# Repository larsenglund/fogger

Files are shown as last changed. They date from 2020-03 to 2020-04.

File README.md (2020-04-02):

# Fogger
A cheap DIY fog machine with automatic temperature control, display and WiFi remote control.

## Hardware
### Bill of materials
The basic fog machine consists of
* Grill lighter, $15
* Copper fuel pipe (6mm outer diameter, 5m long), $22
* Thermocouple thermometer, $4
* Pump (self priming, 6mm outer diameter inlet and outlet, 12V), $4
* 12V adapter, $3
* PVC tube (5mm inner diameter), $3
* Aluminium foil
* Metal wire
* Rockwool insulation
* About 1 liter of sand

Total cost: $51 (assuming you have the last four items on the list, if not rockwool might be the hardest to come by in small quantities)

The upgraded version with automatic temperature control, display and WiFi remote control removes the "manual" thermocouple thermometer and adds these things:
* Wemos D1 mini (ESP8266) $3
* MAX6675/MAX31855 Module + K Type Thermocouple, $5
* 2 channel relay module (3.3V), $3
* 5V charger, $2
* OLED display (0.91", 128x32, I2C), $2
* 10K thermistor + 47k resistor
* Thermal fuse (~150C, 250V, 10A)

Total cost for upgraded version: $62

Fog juice (smoke liquid) is made from
* Destilled water (4L), $4
* Glycerol (1L), $16

Total cost for 5L of 20% fog juice: $20

Fog juice can also be bought premade for about the same price but then you can't vary the concentration as easy.

### Assembly

Some of the stuff needed

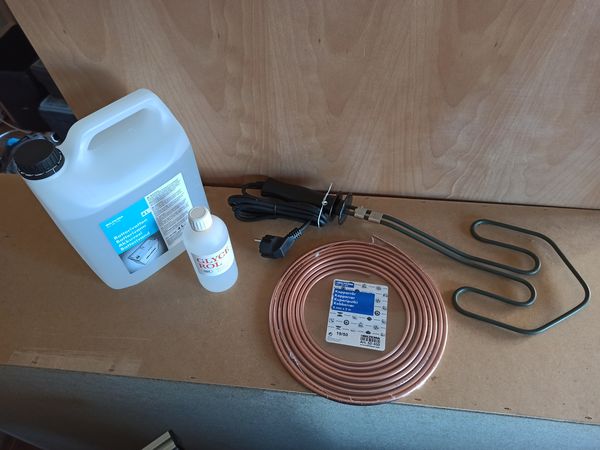
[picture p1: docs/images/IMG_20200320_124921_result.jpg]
Materials


Carefully bend the copper pipe to follow the shape of the grill lighter. Mine was able to go three loops along the whole heater element with a few decimeters to spare on each end. I used cable ties to keep the pipe in place as I was bending it.

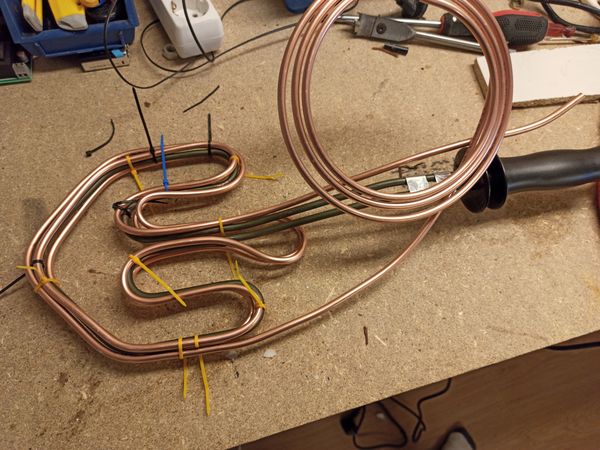
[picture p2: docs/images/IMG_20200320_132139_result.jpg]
Bending


The cable ties are replaced with a tight wiring of metal wire.

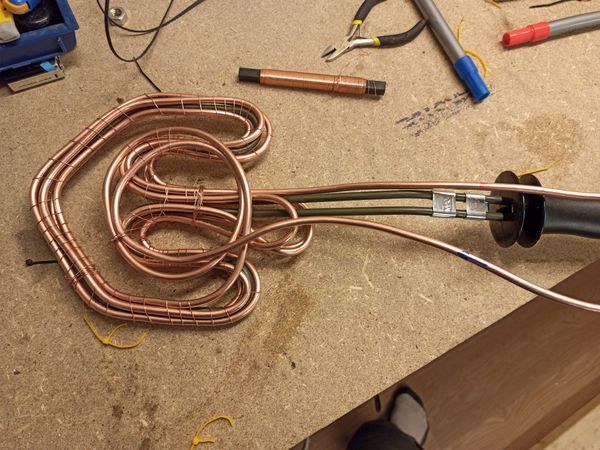
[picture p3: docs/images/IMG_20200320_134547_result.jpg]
Wiring


The thermocouple is wired so that the business end is close to the center of the heater without touching any metal. Then the whole thing is placed on a sheet of rockwool (5-10cm thick) and sand is poured ontop (to act as heat distribution and storage). The rockwool is then folded over to make a insulated package and the whole thing is wrapped in aluminium foil.

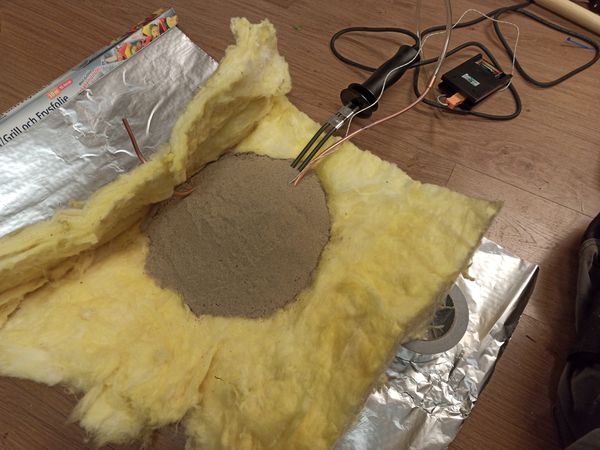
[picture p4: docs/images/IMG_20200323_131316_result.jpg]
Sand


Connect the outlet of the pump to the copper pipe using a PVC tube and on the inled put another tube that leads to a container of fog juice. For the manual version you then plug in the heater and when the temperature reaches 260 degrees celcius on the thermocouple thermometer you can turn off the heater. Turn on power to the pump for a while and enjoy the smoke! When the temperature drops below 250 degrees again you can plug the heater in for a while until it reaches 260 degrees again. The system has quite a bit of thermal lag so if you turn off the heater at 260 degrees it overshoots to about 295 degrees in my setup.

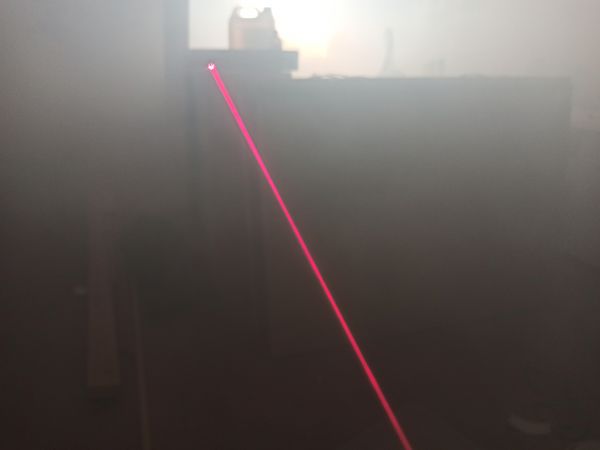
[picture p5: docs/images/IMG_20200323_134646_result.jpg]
Pewpew


Video of first testrun.

(http://www.youtube.com/watch?v=uRvGTlmDHWQ "DIY smoke machine test")

## Electronics
Wiring of components

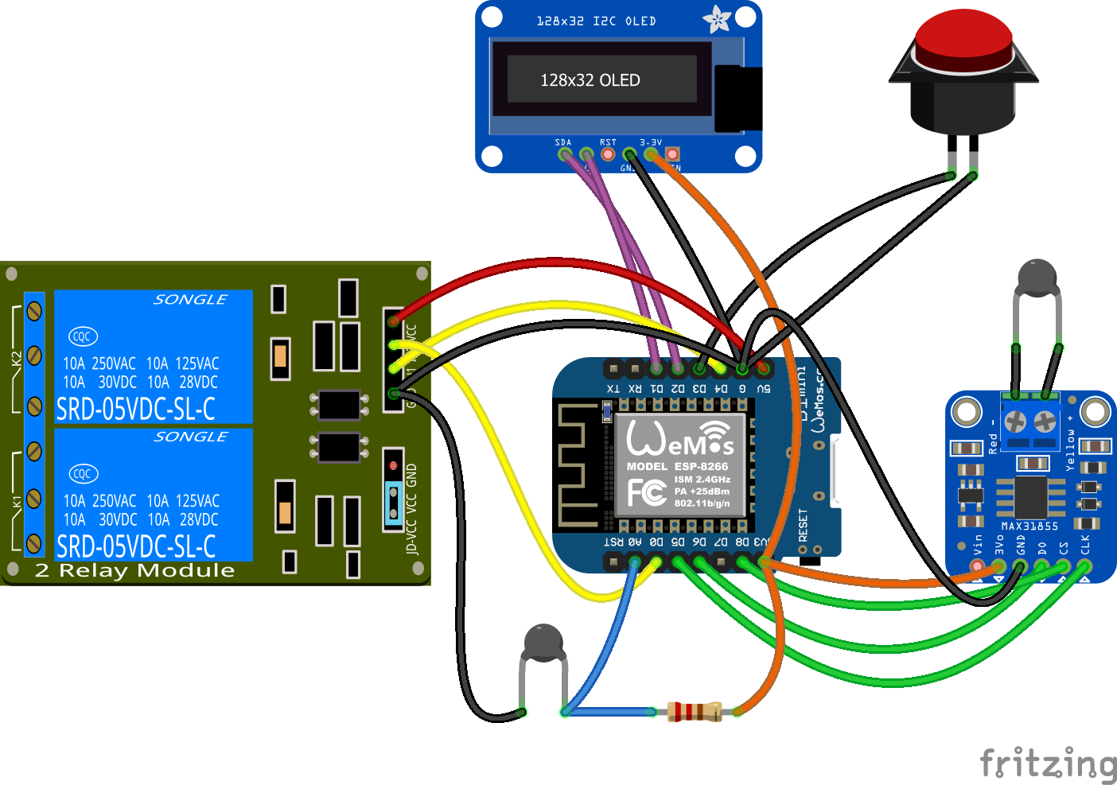
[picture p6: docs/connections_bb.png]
Connections


The heater is connected to channel 1 of the relay board and the pump to channel 2. A 10K thermistor is connected to A0.
The thermal fuse is placed on the incoming live wire.

Pin selection was made using this information.

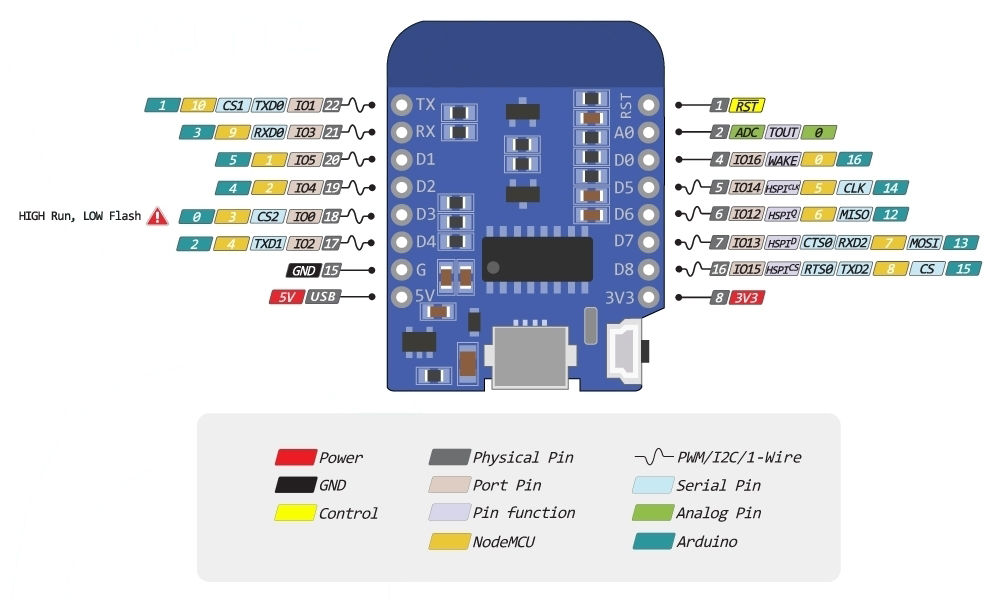
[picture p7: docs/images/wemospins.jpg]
Wemos pins


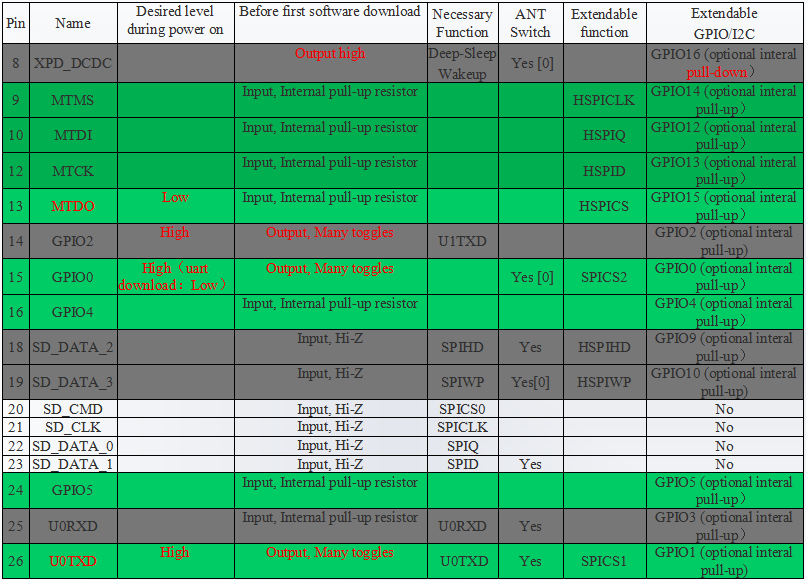
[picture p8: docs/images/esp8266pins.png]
ESP8266 pins


## Software
Software for the Wemos is created with PlatformIO and serves up a captive portal that's used for remote control.

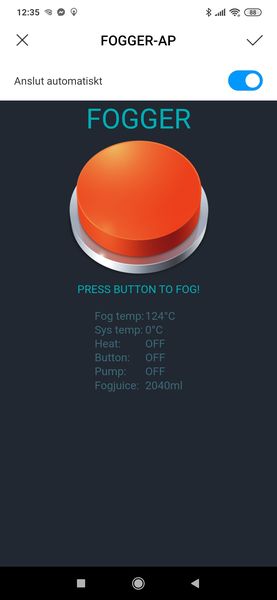
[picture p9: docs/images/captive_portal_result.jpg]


The OLED displays the same information as the captive portal.

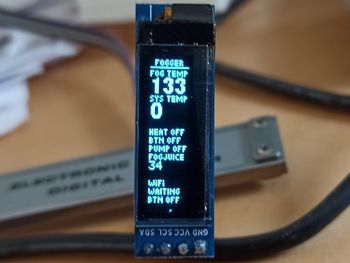
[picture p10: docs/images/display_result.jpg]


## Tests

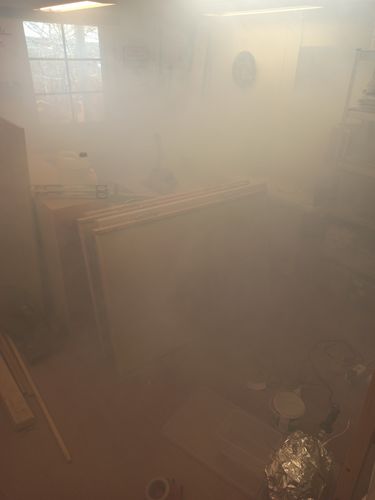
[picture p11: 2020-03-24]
docs/images/IMG_20200323_134607_result.jpg

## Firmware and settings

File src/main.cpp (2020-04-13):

/*
  ESP8266 fog machine controller
  See github for more info https://github.com/larsenglund/fogger
*/

#include <Arduino.h>
#include <math.h>
#include <SPI.h>
#include <Wire.h>
#include <Adafruit_GFX.h>
#include <Adafruit_SSD1306.h>
#include <ESP8266WiFi.h>
#include <DNSServer.h>
#include <FS.h>
#include <ESPAsyncWebServer.h>
#include <WebSocketsServer.h>
#include <Fonts/Picopixel.h>
#include <Fonts/FreeSansBold9pt7b.h>
#include <MAX31855.h>

#define SCREEN_WIDTH 128 // OLED display width, in pixels
#define SCREEN_HEIGHT 32 // OLED display height, in pixels

// Declaration for an SSD1306 display connected to I2C (SDA, SCL pins)
#define OLED_RESET     -1 // Reset pin # (or -1 if sharing Arduino reset pin)

// which analog pin to connect
#define THERMISTORPIN A0  
// resistance at 25 degrees C
#define THERMISTORNOMINAL 10000      
// temp. for nominal resistance (almost always 25 C)
#define TEMPERATURENOMINAL 25   
// how many samples to take and average, more takes longer
// but is more 'smooth'
#define NUMSAMPLES 5
// The beta coefficient of the thermistor (usually 3000-4000)
#define BCOEFFICIENT 3892
// the value of the 'other' resistor
#define SERIESRESISTOR 47090  

#define BUTTON_PIN D3
#define PUMP_PIN D0
#define HEATER_PIN D4

int samples[NUMSAMPLES];

Adafruit_SSD1306 display(SCREEN_WIDTH, SCREEN_HEIGHT, &Wire, OLED_RESET);

volatile bool update_text = true;
volatile bool heater = false;
volatile bool pump = false;
volatile bool button = false;
volatile bool prev_button = false;
volatile bool wifi_button = false;
volatile bool connected = false;
volatile int num_connected = 0;
volatile float fog_temp = 0.0;
volatile float sys_temp = 0.0;
volatile float fogjuice = 0.0;
float fog_upper_temp = 240.0;
float fog_lower_temp = 230.0;
uint32_t test_timestamp;
int prev_x = 0;
int speed = 16; // pixels per second
int prev_timestamp = -1;
int dir = 1;
char buff[16];
int16_t _x1, _y1;
uint16_t w, h;
int32_t rawData = 0;
int delay_count = 0;

MAX31855 myMAX31855(D8);

const char *ssid = "FOGGER-AP";
const char *password =  "fogjuice";
const char *msg_toggle_led = "toggleLED";
const char *msg_get_led = "getLEDState";
const int dns_port = 53;
const int http_port = 80;
const int ws_port = 1337;

IPAddress apIP(192, 168, 4, 1);

DNSServer dnsServer;
AsyncWebServer server(80);
WebSocketsServer webSocket = WebSocketsServer(1337);
char msg_buf[128];
int led_state = 0;

void updateText();
void drawAnimation();
void onWebSocketEvent(uint8_t client_num,
                      WStype_t type,
                      uint8_t * payload,
                      size_t length);
void onIndexRequest(AsyncWebServerRequest *request);
void onPageNotFound(AsyncWebServerRequest *request);

int averageAnalogRead();
float readNTCTemp();


void setup() {
  Serial.begin(115200);

  if( !SPIFFS.begin()){
    Serial.println("Error mounting SPIFFS");
    while(1);
  }

  Dir dir = SPIFFS.openDir("/");
  while (dir.next()) {
      Serial.print(dir.fileName());
      if(dir.fileSize()) {
          File f = dir.openFile("r");
          Serial.println(f.size());
      }
  }

  // Start access point
  WiFi.mode(WIFI_AP);
  WiFi.softAPConfig(apIP, apIP, IPAddress(255, 255, 255, 0));
  WiFi.softAP(ssid, password);
  
  // if DNSServer is started with "*" for domain name, it will reply with
  // provided IP to all DNS request
  dnsServer.start(dns_port, "*", apIP);

  // Print our IP address
  Serial.println();
  Serial.println("AP running");
  Serial.print("My IP address: ");
  Serial.println(WiFi.softAPIP());

  // On HTTP request for root, provide index.html file
  server.on("/", HTTP_GET, onIndexRequest);
  server.on("/fogger", HTTP_GET, onIndexRequest);
  server.on("/generate_204", HTTP_GET, onIndexRequest);
  server.on("/gen_204", HTTP_GET, onIndexRequest);
  server.on("/L0", HTTP_GET, onIndexRequest);
  server.on("/L2", HTTP_GET, onIndexRequest);
  server.on("/ALL", HTTP_GET, onIndexRequest);
  server.on("/bag", HTTP_GET, onIndexRequest);

  server.on("/btn", HTTP_GET, [](AsyncWebServerRequest *request){
    request->send(SPIFFS, "/btn.png", "image/png");
  });
  server.on("/btn_pressed", HTTP_GET, [](AsyncWebServerRequest *request){
    request->send(SPIFFS, "/btn_pressed.png", "image/png");
  });
 
  // Handle requests for pages that do not exist
  server.onNotFound(onPageNotFound);
 
  // Start web server
  server.begin();
 
  // Start WebSocket server and assign callback
  webSocket.begin();
  webSocket.onEvent(onWebSocketEvent);

  // SSD1306_SWITCHCAPVCC = generate display voltage from 3.3V internally
  if(!display.begin(SSD1306_SWITCHCAPVCC, 0x3C)) { // Address 0x3C for 128x32
    Serial.println(F("SSD1306 allocation failed"));
    for(;;); // Don't proceed, loop forever
  }
  display.setRotation(1);
  display.setFont(&Picopixel);
  display.setTextColor(SSD1306_WHITE);
  display.setTextSize(1);
  display.clearDisplay();

  myMAX31855.begin();
  while (myMAX31855.getChipID() != MAX31855_ID)
  {
    Serial.println(F("MAX31855 error")); //(F()) saves string to flash & keeps dynamic memory free
    delay(5000);
  }
  Serial.println(F("MAX31855 OK"));

  switch (myMAX31855.detectThermocouple())
  {
    case MAX31855_THERMOCOUPLE_SHORT_TO_VCC:
      Serial.println(F("Thermocouple short to VCC"));
      break;

    case MAX31855_THERMOCOUPLE_SHORT_TO_GND:
      Serial.println(F("Thermocouple short to GND"));
      break;

    case MAX31855_THERMOCOUPLE_NOT_CONNECTED:
      Serial.println(F("Thermocouple not connected"));
      break;

    case MAX31855_THERMOCOUPLE_UNKNOWN:
      Serial.println(F("Thermocouple unknown error, check spi cable"));
      break;
  }

  if (myMAX31855.detectThermocouple() == MAX31855_THERMOCOUPLE_OK) {
    rawData = myMAX31855.readRawData();

    Serial.print(F("Chip ID: "));
    Serial.println(myMAX31855.getChipID(rawData));

    Serial.print(F("Cold Junction: "));
    Serial.println(myMAX31855.getColdJunctionTemperature(rawData));

    Serial.print(F("Thermocouple: "));
    Serial.println(myMAX31855.getTemperature(rawData));

    fog_temp = myMAX31855.getTemperature(rawData);
  }

  Serial.print("NTC RAW: ");
  Serial.println(analogRead(A0));
  Serial.print("NTC: ");
  sys_temp = readNTCTemp();
  Serial.println(sys_temp);

  pinMode(BUTTON_PIN,INPUT_PULLUP);
  pinMode(PUMP_PIN,OUTPUT);
  pinMode(HEATER_PIN,OUTPUT);

  test_timestamp = millis()+1000;
}

void loop() {

  if (update_text) {
    update_text = false;
    display.clearDisplay();
    updateText();
    sprintf(msg_buf, "%d %d %d %d %d %d", (int)fog_temp, (int)sys_temp, heater, pump, (int)fogjuice, button);
    Serial.printf("Broadcasting: %s\n", msg_buf);
    webSocket.broadcastTXT(msg_buf);
    //display.drawRect(0, 0, display.width(), display.height(), SSD1306_WHITE); // draw fullscreen rect to help align the deplay in its enclosure
  }

  dnsServer.processNextRequest();
  webSocket.loop();
  drawAnimation();

  if (++delay_count > 10) {
    delay_count = 0;
    if (myMAX31855.detectThermocouple() == MAX31855_THERMOCOUPLE_OK) {
      rawData = myMAX31855.readRawData();
      float new_temp = myMAX31855.getTemperature(rawData);
      if (new_temp > 800) {
        new_temp = fog_temp;
      }
      if ((int)new_temp != (int)fog_temp) {
        fog_temp = new_temp;
        if (fog_temp > fog_upper_temp) {
          heater = false;
        }
        if (fog_temp < fog_lower_temp) {
          heater = true;
        }
        update_text = true;
      }
    } else {
      heater = false;
      update_text = true;
    }
    if (sys_temp > 90.0) {
      heater = false;
      update_text = true;
    }

    if ((int)readNTCTemp() != (int)sys_temp) {
      sys_temp = readNTCTemp();
      update_text = true;
    }
  }

  /*if (test_timestamp < millis()) {
    test_timestamp = millis() + 1000;
    fog_temp = (fog_temp + 1.0);
    if (fog_temp > 300) fog_temp = 0;
    fogjuice = (fogjuice + 0.3);
    if (fogjuice > 5000) fogjuice = 0;
    update_text = true;
  }*/

  button = !digitalRead(BUTTON_PIN);
  if (button != prev_button) {
    Serial.print("Button: ");
    Serial.println(button);
    Serial.print("WiFi button: ");
    Serial.println(wifi_button);
    prev_button = button;
    update_text = true;
  }

  pump = (button || wifi_button);

  digitalWrite(PUMP_PIN, !pump);
  digitalWrite(HEATER_PIN, !heater);

  display.display();
  delay(50);
}

int averageAnalogRead() {
  int val = 0;
  for(int i = 0; i < 20; i++) {
    val += analogRead(A0);
    delay(1);
  }
  return val / 20;
}

float readNTCTemp() {
  // Thermistor code from https://learn.adafruit.com/thermistor/using-a-thermistor
  uint8_t i;
  float average;
 
  // take N samples in a row, with a slight delay
  for (i=0; i< NUMSAMPLES; i++) {
   samples[i] = analogRead(THERMISTORPIN);
   delay(10);
  }
  
  // average all the samples out
  average = 0;
  for (i=0; i< NUMSAMPLES; i++) {
     average += samples[i];
  }
  average /= NUMSAMPLES;
 
  //Serial.print("Average analog reading "); 
  //Serial.println(average);
  
  // convert the value to resistance
  average = 1023 / average - 1;
  average = SERIESRESISTOR / average;
  //Serial.print("Thermistor resistance "); 
  //Serial.println(average);
  
  float steinhart;
  steinhart = average / THERMISTORNOMINAL;     // (R/Ro)
  steinhart = log(steinhart);                  // ln(R/Ro)
  steinhart /= BCOEFFICIENT;                   // 1/B * ln(R/Ro)
  steinhart += 1.0 / (TEMPERATURENOMINAL + 273.15); // + (1/To)
  steinhart = 1.0 / steinhart;                 // Invert
  steinhart -= 273.15;                         // convert to C
  
  //Serial.print("Temperature "); 
  //Serial.print(steinhart);
  //Serial.println(" *C");

  return steinhart;
}

void drawAnimation() {
  int now = millis();
  if (prev_timestamp < 0) {
    prev_timestamp = millis();
  }
  int step = (now - prev_timestamp) * speed / 1000;
  int x = prev_x + step*dir;
  if (x >= display.width()) { // right bounce
    dir = -1;
    x = prev_x + step*dir;
  }
  else if (x < 0) { // left bounce
    dir = 1;
    x = prev_x + step*dir;
  }
  display.drawPixel(prev_x, display.height()-1, SSD1306_BLACK);
  display.drawPixel(x, display.height()-1, SSD1306_WHITE);
  prev_x = x;
  prev_timestamp = now;
}

void updateText() {
  display.setCursor(4,5);
  display.println(F("FOGGER"));
  //display.println();
  display.drawLine(0,7,32,7,SSD1306_WHITE);
  display.setCursor(0,14);

  display.println(F("FOG TEMP"));
  display.println();
  display.setFont(&FreeSansBold9pt7b);
  display.print(fog_temp, 0);
  //display.print((char)247);
  //display.println("C");
  display.setFont(&Picopixel);
  display.println();
  display.println(F("SYS TEMP"));
  display.println();
  display.setFont(&FreeSansBold9pt7b);
  //sprintf(buff, "%d", (int)round(sys_temp));
  //display.getTextBounds(buff, 0, 0, &_x1, &_y1, &w, &h); //calc width of new string
  display.print(sys_temp, 0);
  //display.setCursor(display.getCursorX() + (display.width() - w) / 2, display.getCursorY());
  //display.print(buff);
  display.setFont(&Picopixel);
  display.println();
  display.println();

  display.print(F("HEAT "));
  display.println((heater?"ON":"OFF"));

  display.print(F("BTN "));
  display.println((button?"ON":"OFF"));

  display.print(F("PUMP "));
  display.println((pump?"ON":"OFF"));

  display.print(F("FOGJUICE"));
  //display.println();
  display.setFont();
  display.println();
  display.print(fogjuice, 0);
  display.setFont(&Picopixel);
  display.println();

  //display.print((char)247);
  //isplay.println("C");

  /*display.drawRect(104, 0, 15, 15, SSD1306_WHITE);
  if (connected) {
    display.fillRect(106, 2, 11, 11, SSD1306_WHITE);
  }
  display.setCursor(101,16);
  display.println("WiFi");*/
  display.println();
  display.println(F("WiFi"));
  display.println((num_connected>0?"ACTIVE":"WAITING"));
  display.print(F("BTN "));
  display.println((wifi_button?"ON":"OFF"));
}

// Callback: receiving any WebSocket message
void onWebSocketEvent(uint8_t client_num,
                      WStype_t type,
                      uint8_t * payload,
                      size_t length) {
 
  // Figure out the type of WebSocket event
  switch(type) {
 
    // Client has disconnected
    case WStype_DISCONNECTED:
      Serial.printf("[%u] Disconnected!\n", client_num);
      num_connected --;
      break;
 
    // New client has connected
    case WStype_CONNECTED:
      {
        IPAddress ip = webSocket.remoteIP(client_num);
        Serial.printf("[%u] Connection from ", client_num);
        Serial.println(ip.toString());
        num_connected ++;
      }
      break;
 
    // Handle text messages from client
    case WStype_TEXT:
 
      // Print out raw message
      Serial.printf("[%u] Received text: %s\n", client_num, payload);
 
      // Toggle LED
      if ( strcmp((char *)payload, "toggleLED") == 0 ) {
        led_state = led_state ? 0 : 1;
        Serial.printf("Toggling LED to %u\n", led_state);
        digitalWrite(LED_BUILTIN, led_state);
 
      // Report the state of the LED
      } else if ( strcmp((char *)payload, "getState") == 0 ) {
        sprintf(msg_buf, "%d %d %d %d %d %d", (int)fog_temp, (int)sys_temp, heater, pump, (int)fogjuice, button);
        Serial.printf("Sending to [%u]: %s\n", client_num, msg_buf);
        webSocket.sendTXT(client_num, msg_buf);
 
      // Message not recognized
      } else if ( strcmp((char *)payload, "fogDown") == 0 ) {
        wifi_button = true;

      } else if ( strcmp((char *)payload, "fogUp") == 0 ) {
        wifi_button = false;

      } else {
        Serial.println("[%u] Message not recognized");
      }
      break;
 
    // For everything else: do nothing
    case WStype_BIN:
    case WStype_ERROR:
    case WStype_FRAGMENT_TEXT_START:
    case WStype_FRAGMENT_BIN_START:
    case WStype_FRAGMENT:
    case WStype_FRAGMENT_FIN:
    default:
      break;
  }
  update_text = true;
}

// Callback: send homepage
void onIndexRequest(AsyncWebServerRequest *request) {
  IPAddress remote_ip = request->client()->remoteIP();
  Serial.println("[" + remote_ip.toString() +
                  "] HTTP GET request of " + request->url());
  request->send(SPIFFS, "/index.html", "text/html");
}
 
// Callback: send 404 if requested file does not exist
void onPageNotFound(AsyncWebServerRequest *request) {
  IPAddress remote_ip = request->client()->remoteIP();
  Serial.println("[" + remote_ip.toString() +
                  "] HTTP GET request of " + request->url());
  request->send(404, "text/plain", "Not found");
}

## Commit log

2020-03-26 Added nicer web UI and two way websocket data flow
2020-03-27 Added some documentation
    [connections.fzz]
2020-03-27 Added thermistor for system ambient temperature sensing
    [connections.fzz]
2020-04-01 Updated code for thermistor, thermocouple, button and relays.
2020-04-01 Added automatic temperature control of the heater
2020-04-01 Added basic overheat protection
    [main.cpp]
2020-04-01 Added heater control
